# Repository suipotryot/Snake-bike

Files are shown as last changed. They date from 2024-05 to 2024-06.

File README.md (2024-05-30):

# Qu'est ce que c'est ?
Le Snake-bike est un tricycle compact et léger qui permet de rouleur seul et qui peut être accroché à n'importe quel autre Snake-bike, voire même plusieurs, pour devenir un plus grand véhicule. Cela donne une chaîne de vélos articulée qui se déplace telle un serpent, fluide et rapide.

## Pourquoi le Snake bike ?
Le constat généralement fait à propos des transports est que la voiture est omniprésente et qu'il n'y a pas vraiment d'alternative viable. Mais la plupart des réponses à cette problématique sont de nouvelles voitures plus petites, plus légères et électriques ; ou alors de plus gros vélos pour transporter plus de monde, ce qui nécessite également une électrification pour aider le "pédaleur" qui fournit l'énergie pour tout le monde.

Le Snake-bike propose une approche différente : on peut rouler seul et dans ce cas, on ne transporte que son propre véhicule, rien de plus ; mais on peut également rouler à plusieurs sans pour autant s'équiper d'un autre véhicule. Une forme de multi-modalité douce.

En plus de cela, le Snake-bike, outre son cadre spécifique, n'est composé que d'éléments de vélo standards.

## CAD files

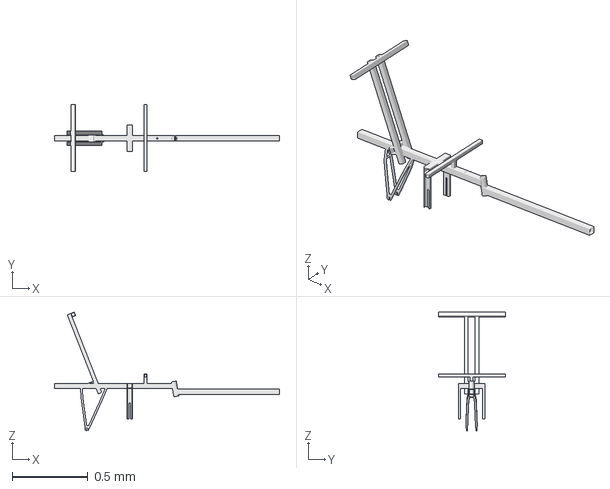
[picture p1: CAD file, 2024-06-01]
Couleuvre.FCStd
1.48 x 0.44 x 0.783 mm

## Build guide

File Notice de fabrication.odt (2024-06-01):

Guide de fabrication du cadre du Snake bike

Modèle Couleuvre – Version Mai 2024

# Le cadre

## Matériel nécessaire

- C1 - tube acier section carrée, diamètre 35 mm, épaisseur 3 mm, L = 1000 mm (partie arrière) ;
- C2 - tube acier section carrée, diamètre 35 mm, épaisseur 3 mm, L = 600 mm (partie avant) ;
- C3 - tube acier section carrée, diamètre 35 mm, épaisseur 3 mm, L = 400 mm (support Nexus) ;
- C4 - tube acier section carrée, diamètre 20 mm, épaisseur 2 mm, L = 500 mm ;
- C5 - tube acier section carrée, diamètre 40 mm, épaisseur 2 mm, L = 105 mm ;
- C6 - tube acier rond, diamètre 34 mm, L= 100 mm (tube de potence standard) ;
- C7 - triangle arrière de vélo 16 pouce en acier.

## Étapes de fabrication

1. Découper les tubes C1 et C2 de manière à ce qu'ils épousent la forme du tube C6 en lui donnant un angle de 10°.
2. Souder les tubes C1 et C2 sur C6 selon le schéma 1. (https://wikixd.fabmob.io/Fichier:SD_Etape_1_-_Soudure_C1_C2_et_C6.png)

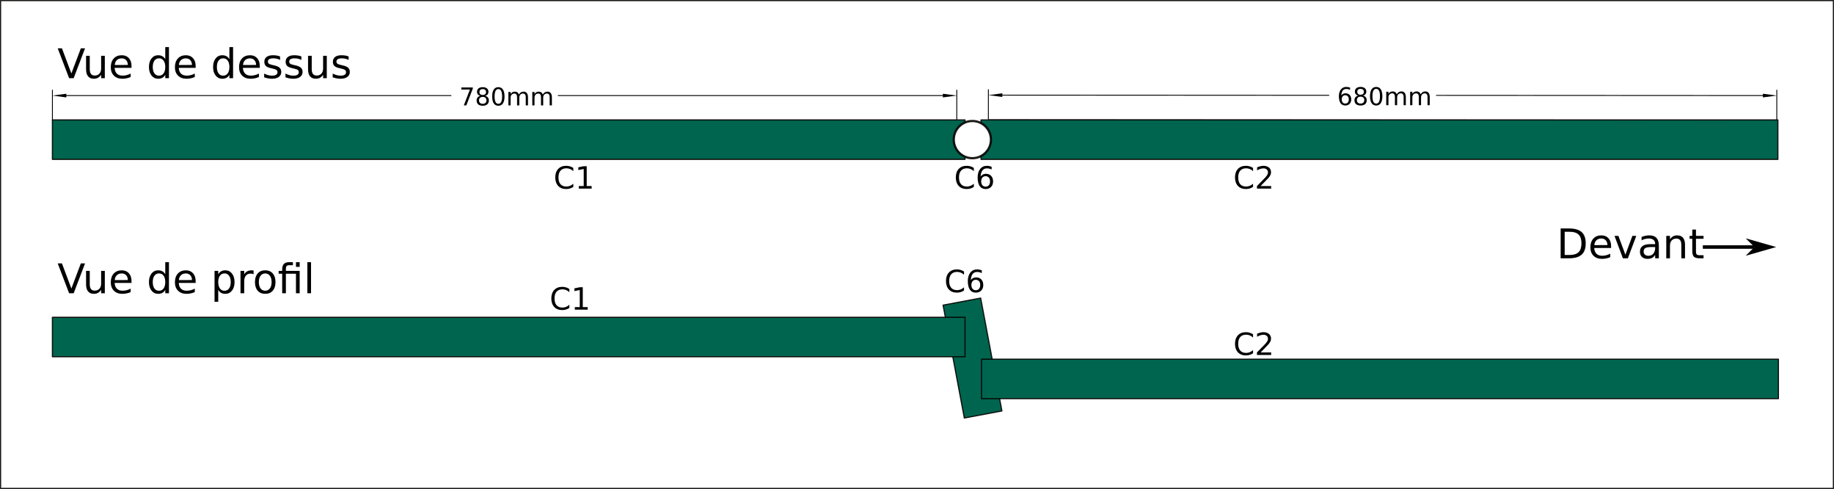
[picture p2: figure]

3. Percer un trou vertical de diamètre 10 mm dans la partie arrière, à ? mm de la potence (pour le guidon).
4. Percer un trou horizontal de diamètre 10 mm dans la partie arrière, à ? mm de la potence (pour la partie arrière du siège).
5. Percer deux trous de diamètre 8 mm dans la partie avant, à 385 mm de la potence (pour le support de pédalier). Cette distance est adaptée à quelqu’un de plutôt grand (1m80) et est à adapter.
6. Percer deux trous de diamètre 10 mm dans la partie avant, à ? mm de la potence (pour le tendeur de chaîne).
7. Percer un trou de diamètre 18 mm dans la partie arrière à 640 mm de la potence. Ce trou servira à fixer la boule de remorquage.

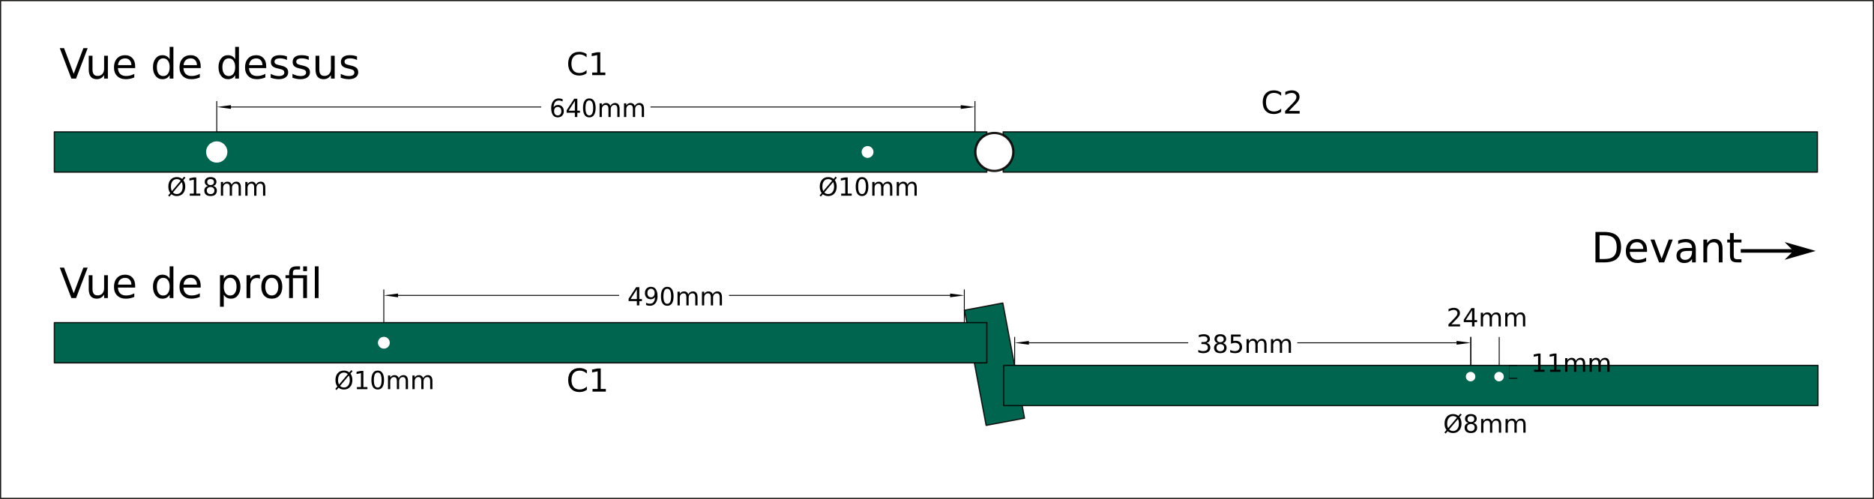
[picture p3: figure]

  (https://wikixd.fabmob.io/Fichier:SD_Etape_2_-_Trous_C1_et_C2.png)
8. Souder le triangle de vélo C7 sur la structure. (https://wikixd.fabmob.io/Fichier:SD_Schéma_3_-_Soudure_triangle_vélo.png)

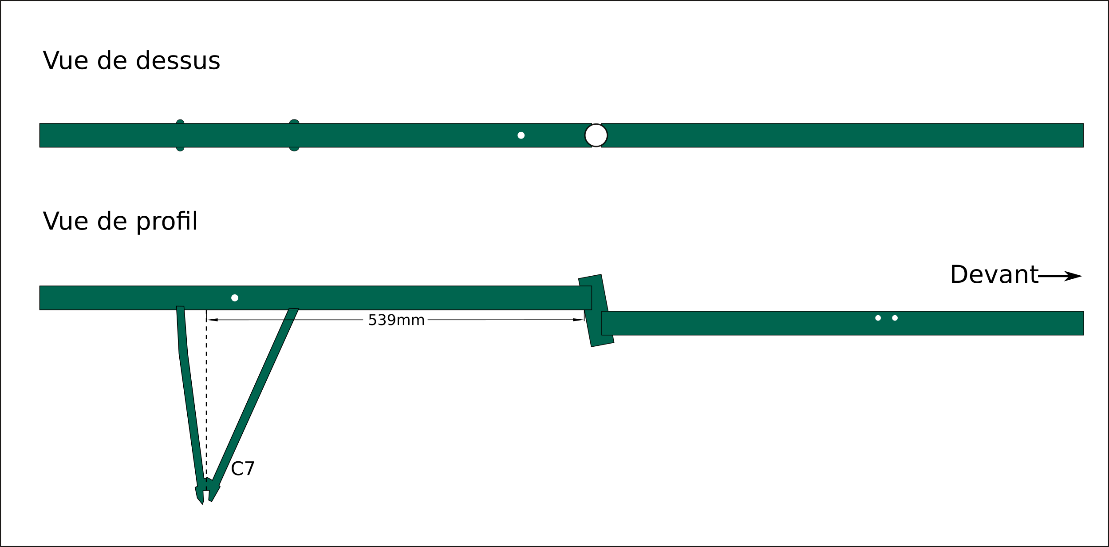
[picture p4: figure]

9. Découper le tube C4 en une section de 440 mm et une de 40 mm. Les souder en formant un "T".
10. Souder ce "T" sur le cadre à 160 mm de la potence. (https://wikixd.fabmob.io/Fichier:SD_Schéma_4_-_Soudure_T_du_siège.png)

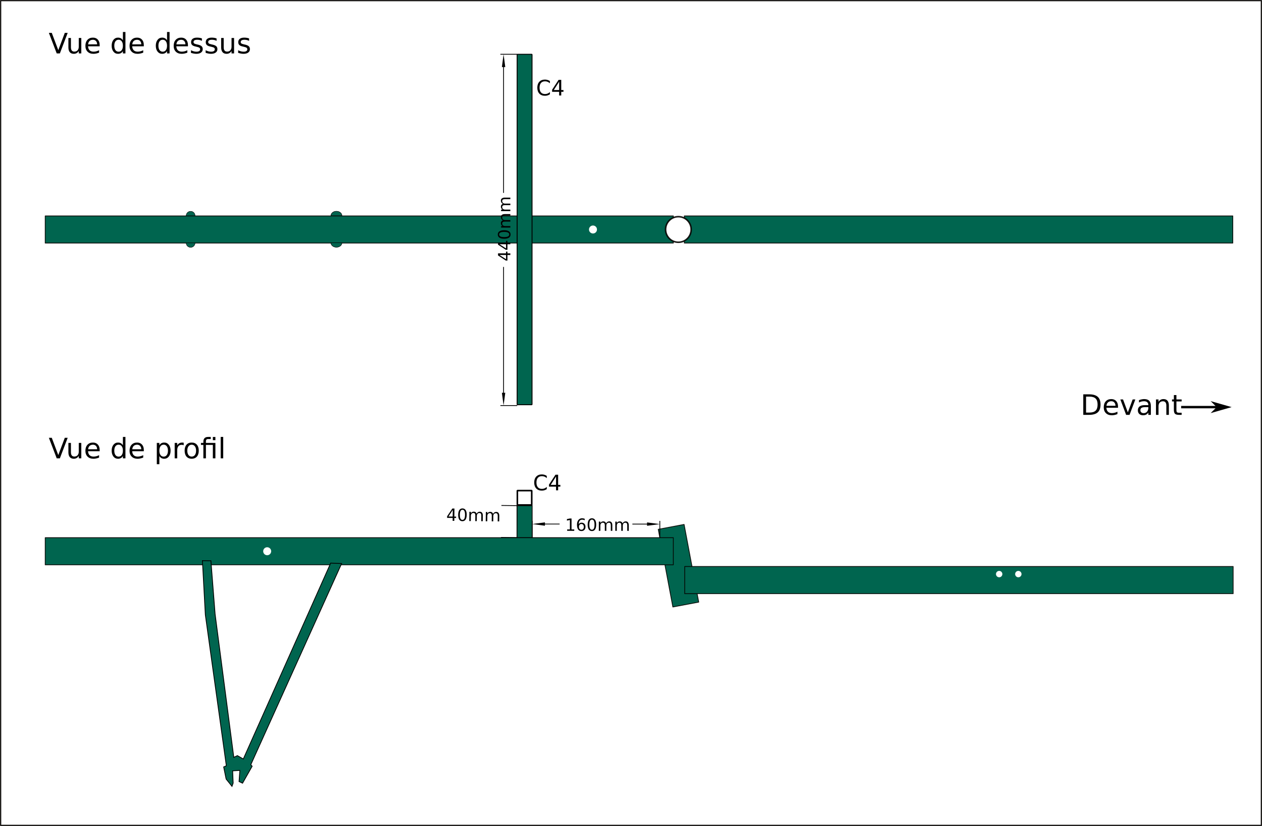
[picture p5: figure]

11. Découper le tube C5 sur la longueur pour obtenir un "L" qui servira de butée au siège.
12. Souder ce "L" sur le cadre. (https://wikixd.fabmob.io/Fichier:Schéma_5_-_Soudure_butée_du_siège.png)

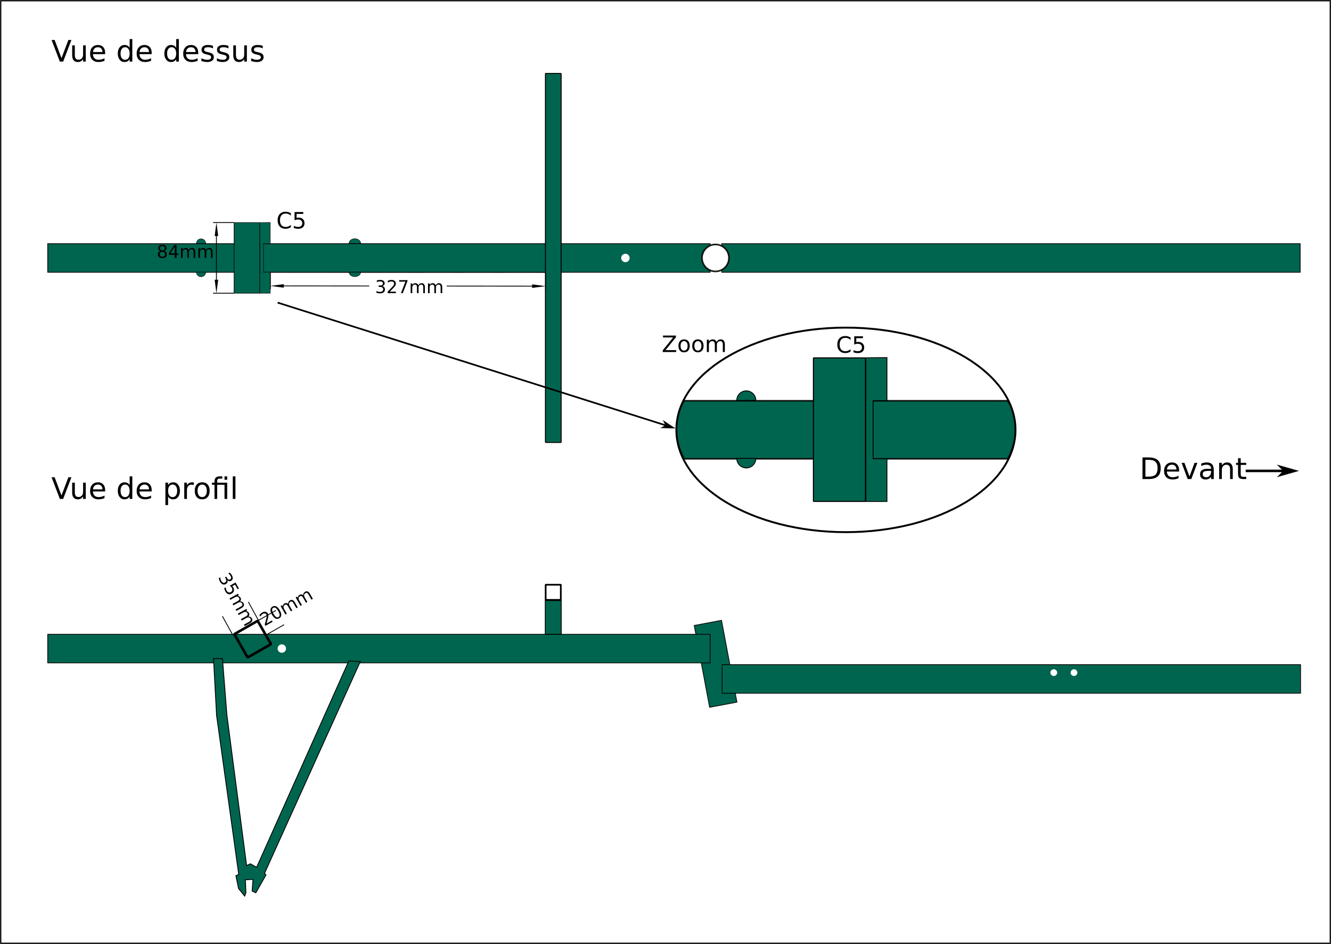
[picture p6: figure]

13. Découper le tube C3 en deux parties de 70 mm et une de 200 mm.
14. Couper la partie de 200 mm en deux sur la longueur et y découper une entaille de 10 mm de large sur deux tiers de sa longueur, en son centre (cela permettra de régler la position du Nexus).
15. Souder le tout sur le cadre pour qu'il y ait un écart de 133 mm entre les deux pièces verticales.

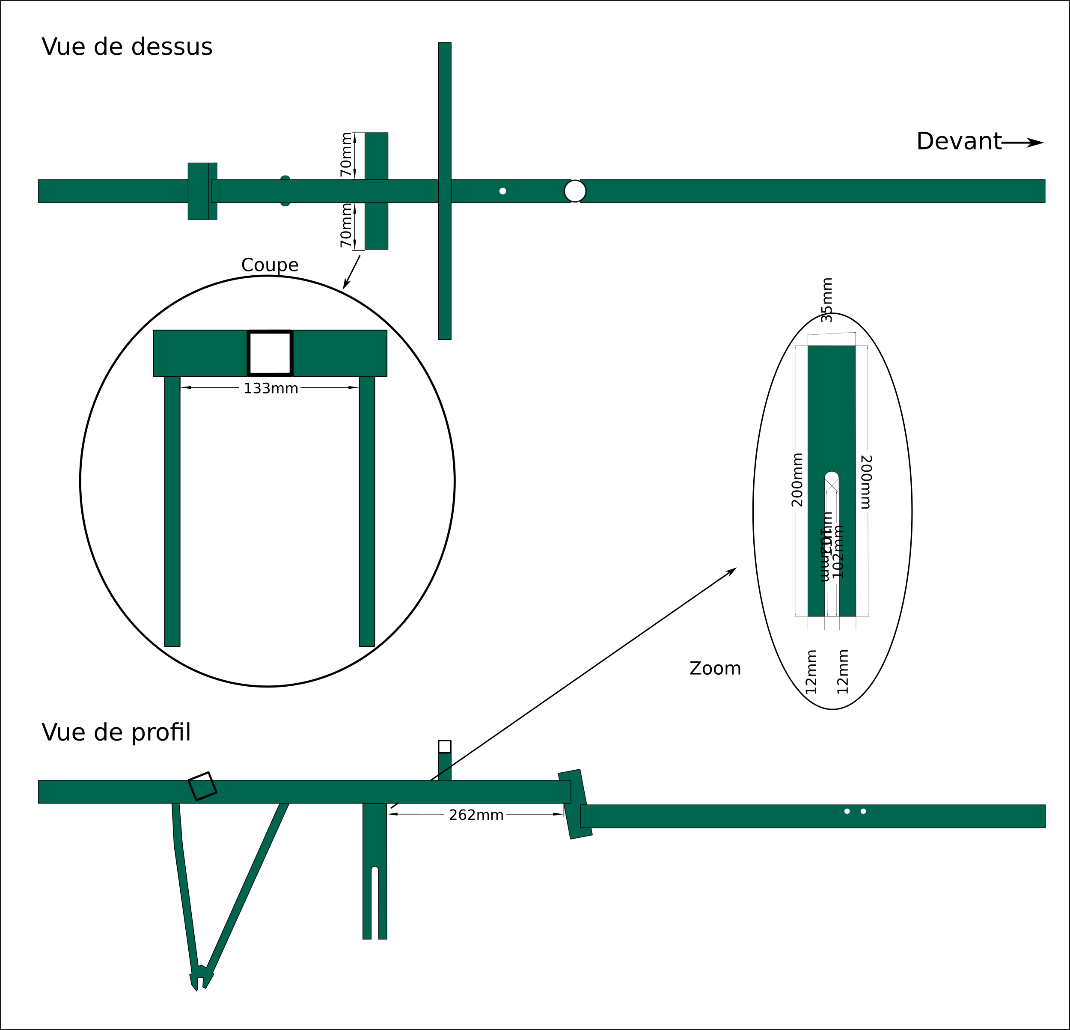
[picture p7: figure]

  (https://wikixd.fabmob.io/Fichier:SD_Schéma_6_-_Soudure_structure_Nexus.png)

Voilà ! Après ces étapes, le cadre est terminé et on en a presque fini avec les soudures.

# Direction - Guidon

## Matériel nécessaire

- G1 - tube acier section rectangle, diamètre 20x30 mm, épaisseur 2 mm, L = 600 mm ;
- G2 - Un guidon pour VTT en acier.

## Étapes de fabrication

1. Percer un trou de diamètre 10 mm en centre de G1 (sur le côté de 30 mm).
2. Percer un second trou de diamètre 8 mm à 100 mm du premier.
3. Couper le guidon G2 en deux parties égales.
4. Souder les deux parties de G2 aux extrémités de G1. Bien veiller à ce que les deux parties soient orientées dans le même sens. (https://wikixd.fabmob.io/Fichier:SD_Schéma_7.1_-_Soudure_et_percement_Guidon.png)

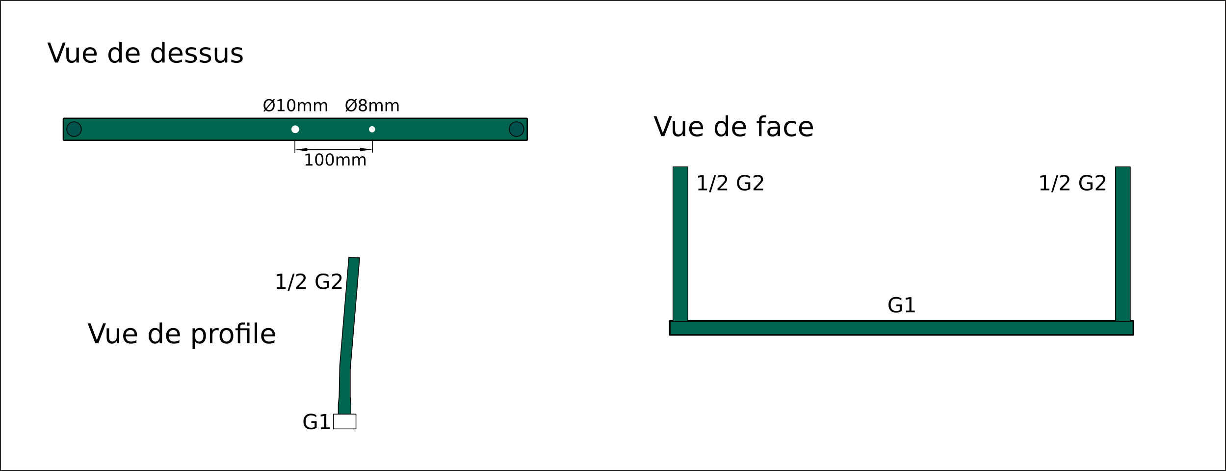
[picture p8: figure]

5. Monter le guidon sur le trou prévu dans le cadre. (https://wikixd.fabmob.io/Fichier:SD_Schéma_7.2_-_Montage_Guidon.png)

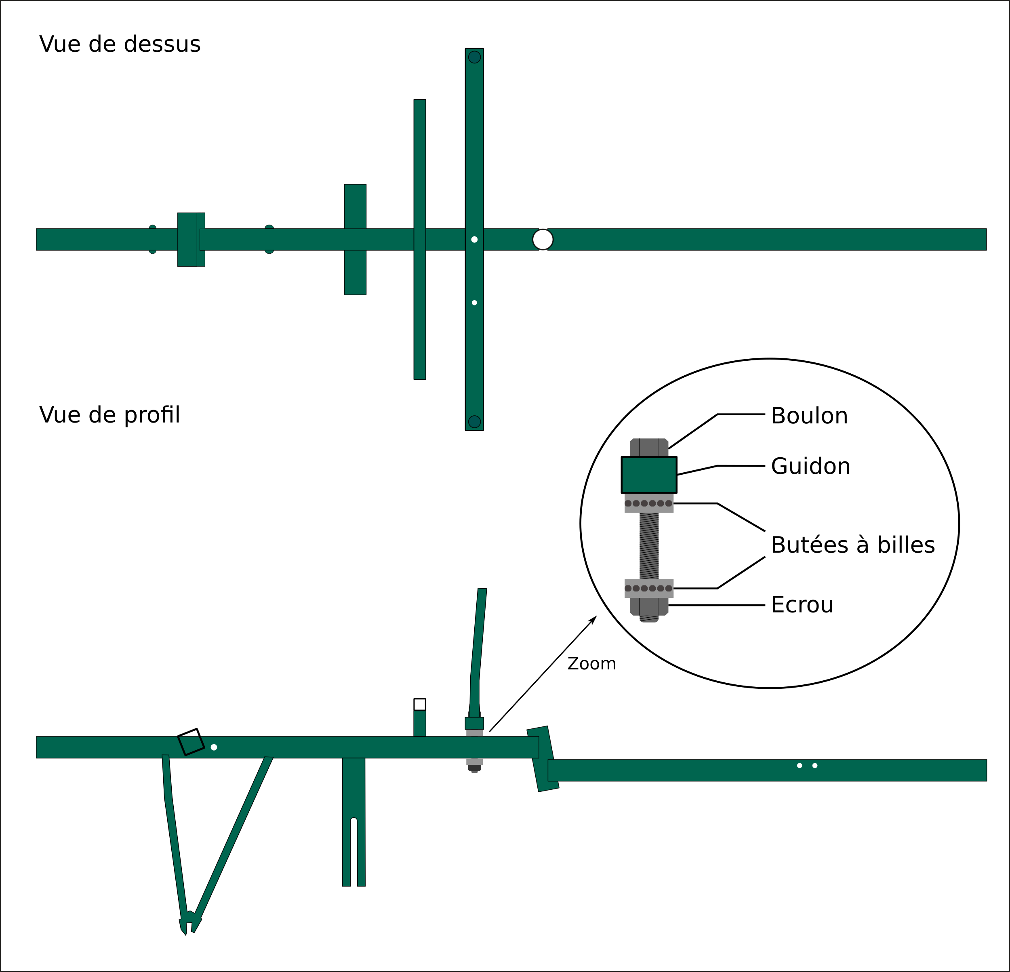
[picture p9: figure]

# Direction - Contrôle

## Matériel nécessaire

- DC1 - Tige de direction se serrant dans la potence.
- DC2 - Barre acier d'épaisseur 5 mm et de largeur 25 mm, L = 100 mm.

## Étapes de fabrication

1. Couper la tige DC1 pour avoir 90 mm entre la pointe et le bord.
2. Souder la barre DC2 sur la partie droite de la tige DC1.
3. Percer de trous de diamètre 8 mm dans DC2, un au milieu de là ou est soudée DC1 et l'autre 70 mm plus loin.

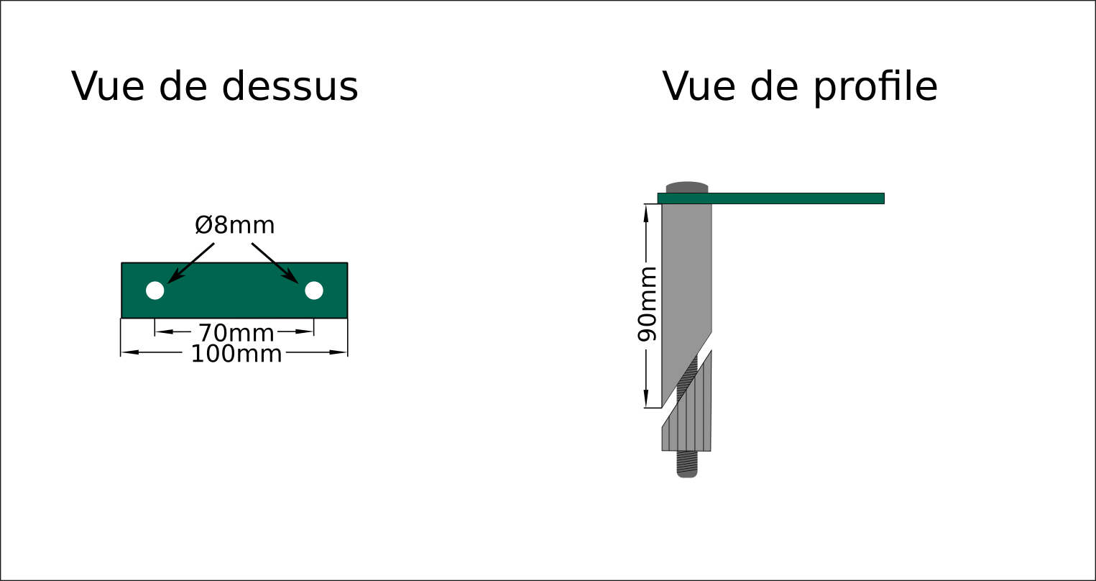
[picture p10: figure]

(https://wikixd.fabmob.io/Fichier:SD_Schéma_8_-_Soudure_contrôle_de_direction.png)

# Direction - Montage

## Matériel nécessaire

- DM1 - Rotule DIN de diamètre 8 mm.
- DM2 - Rotule TSF de diamètre 8 mm.
- DM3 - Deux butées à billes de diamètre intérieur 10 mm.
- DM4 - Un boulon de diamètre 10 mm et de longueur ? mm.
- DM5 - Un écrou à arrêt pour boulon de 10 mm.
- DM6 - Un boulon de diamètre 8 mm et de longueur 40 mm.
- DM7 - Un écrou à arrêt pour boulon de 8 mm.
- DM8 - Tige filetée diamètre 8 mm, L = 80 mm.

## Étapes de fabrication

1. Fixer le guidon de direction sur le cadre grâce au boulon DM4 en faisant un sandwich : Guidon / butée à bille DM3 / cadre / butée à bille DM3 / écrou d'arrêt DM5.
2. Fixer la rotule DIN DM1 dans le trou du contrôle de direction.
3. Fixer la rotule TSF DM2 dans le trou du guidon avec le boulon DM6 et l'écrou DM7.
4. Relier les deux rotules avec la tige filetée DM8.

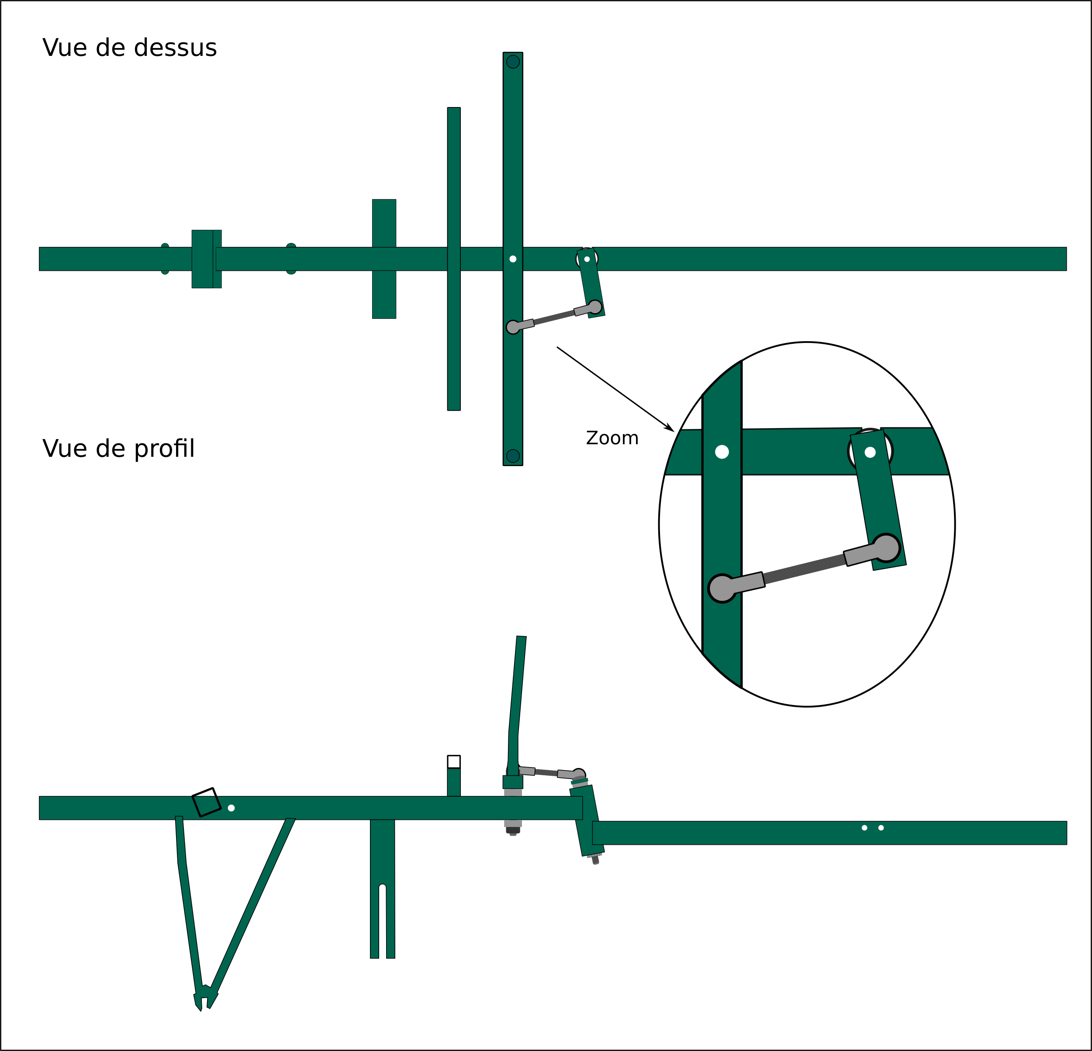
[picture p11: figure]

(https://wikixd.fabmob.io/Fichier:SD_Schéma_9_-_Rotules_de_direction.png)

La direction est prête \o/.

# Siège

## Matériel nécessaire

- S1 - 2 tubes alu carré diamètre 25 mm, L = ? mm.
- S2 - Tube alu carré diamètre 25 mm, L = 440 mm.
- S3 - 2 boulons + écrous + rondelles 5*60 mm.
- S4 - Boulon 10*120 mm + écrou.
- S5 - Deux butées à billes de diamètre intérieur 10 mm.
- S6 - Tissu pour chilienne, 800 x 440 mm.
- S7 - Rivets 3 mm.

## Étapes de fabrication

1. Percer les deux tubes S1 en bas en 10 mm et en haut en 6 mm.
2. Percer deux trous dans le tube S2 en diamètre 6 mm à 180 mm de chaque côté.
3. Boulonner les trois tubes ensemble.
4. Fixer au cadre avec le boulon S4 et les deux butées à bille S5. (https://wikixd.fabmob.io/Fichier:SD_Schéma_10.1_-_Tubes_de_siège.png)

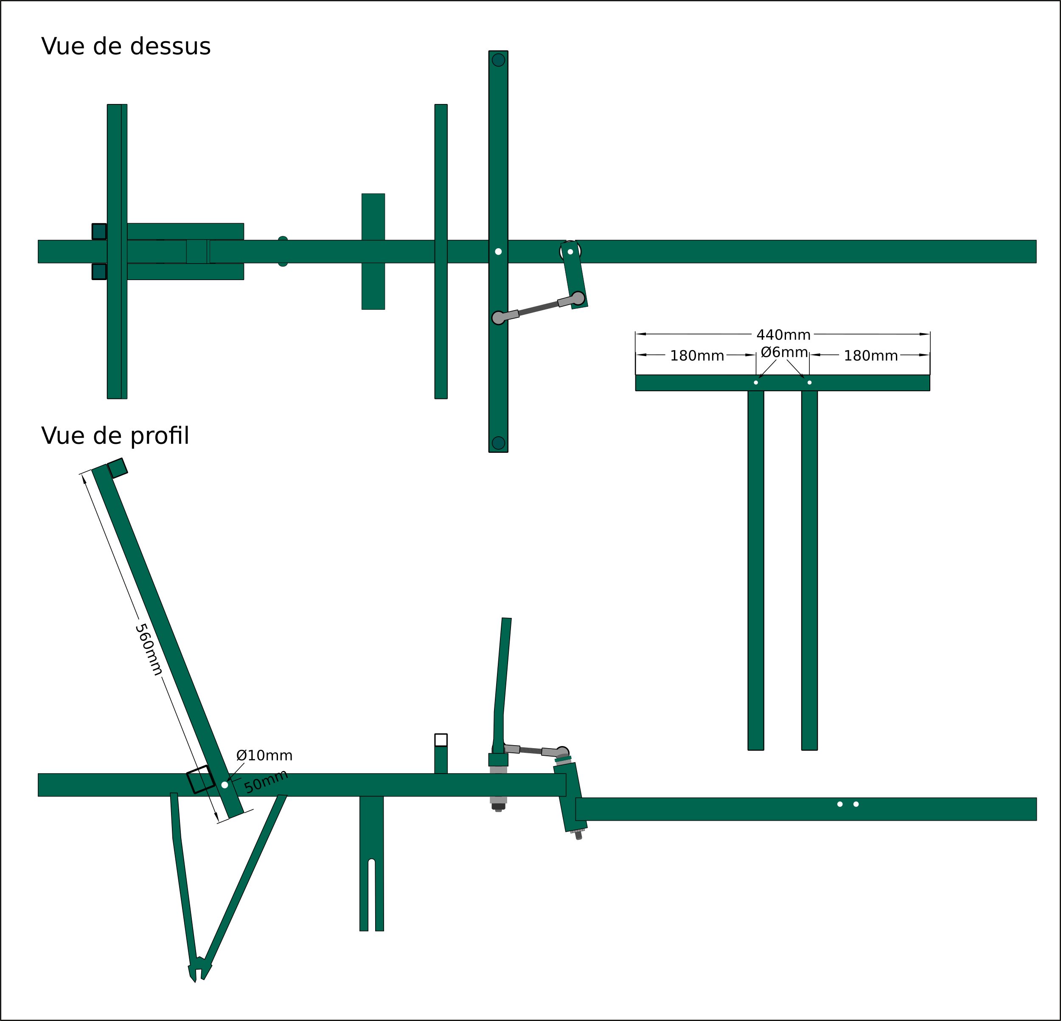
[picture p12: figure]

5. Riveter le tissu S6 avec les rivets S7 de part et d'autre du support de siège. (https://wikixd.fabmob.io/Fichier:SD_Schéma_10.2_-_Tissu_de_siège.png)

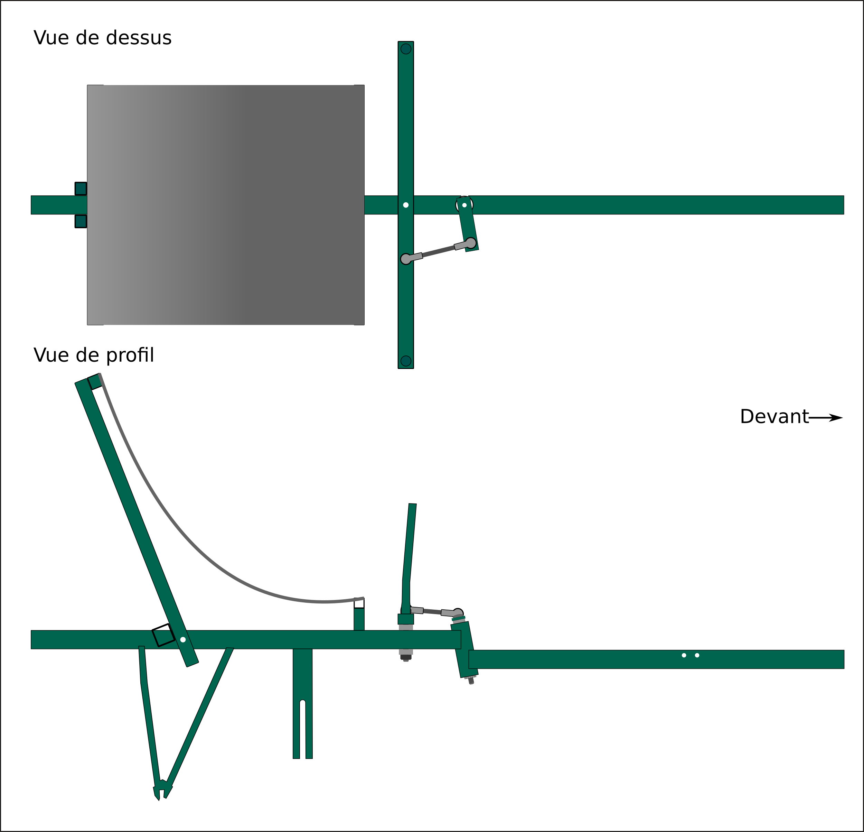
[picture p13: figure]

# Propulsion

## Matériel nécessaire

- P1 - Kit pour tricycle.
- P2 - Boulon + écrous diamètre 10 mm, L = ? mm.
- P3 - Boulon + écrous diamètre 10 mm, L = ? mm.
- P4 - Nexus inter 8 ou moins, selon les goûts).
- P5 - pignon de pédalier récupéré de 28 dents.
- P6 - boulons 3x10 mm + écrous + écrous d'arrêt.
- P7 - Support pour pédalier.
- P8 - Pédalier.
- P9 - 2 chaînes de vélo.

## Étapes de fabrication

1. Installer le kit P1 grâce aux boulons P2 et P3. Régler l'écart avec des écrous.
2. Découper le pignon P5 pour pouvoir le fixer au Nexus (c'est l'étape la plus fastidieuse de la fabrication).
3. Percer le pignon P5 en s'assurant de bien l'aligner avec les trous du Nexus (utiliser un patron en carton).
4. Fixer le pignon au Nexus via les boulons P6 en mettant à chaque fois 3 petits écrous entre le Nexus et le pignon.
5. Monter la cassette du Nexus en veillant bien à mettre le pignon du Nexus vers l'extérieur (pour l'éloigner le plus possible du pignon fait maison).
6. Installer le Nexus sur le cadre, cassette vers le bas.
7. Boulonner le support P7.
8. Fixer le pédalier P8 sur P7.
9. Installer une chaîne de vélo P9 entre le pédalier et le pignon d'origine du Nexus.
10. Installer la seconde chaîne P9 entre le pignon fait maison P5 du Nexus et le kit pour tricycle P1.

Après ajout des éléments de cycle (freins, levier de vitesse, gaines et câbles associés), le Snake est prêt pour rouler en solo !

Attention néanmoins, la version solitaire du Snake bike est un peu déséquilibrée et n’est pas faite pour de grandes vitesses ni des virages trop serrés.

# Système de chaînage

## Matériel nécessaire

- CH1 - Boîtier d'attelage pour tube carré 50 mm
- CH2 - Rotule spéciale quad diamètre 50 mm.

## Étapes de fabrication

1. Fixer CH1 à l'avant du Snake.
2. Fixer CH2 à l'arrière.

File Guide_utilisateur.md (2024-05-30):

# Guide de l’utilisateur du Snake-bike

## Avant propos

À l’heure actuelle, le Snake-bike reste à l’état de prototype. Son utilisation n’a pas encore été suffisamment éprouvée pour permettre d’assurer sa fiabilité, notamment pour des vitesses supérieures à 15km/h et pour de longues distances.

Bien que particulier et original, le Snake-bike est un vélo à part entière. Il entre légalement dans la catégorie des cycles, que l’on retrouve officiellement dans l’article R311-1 du code de la  route (https://www.legifrance.gouv.fr)
« 6.10. Cycle : véhicule ayant au moins deux roues et propulsé exclusivement par l’énergie musculaire des personnes se trouvant sur ce véhicule, notamment à l’aide de pédales ou de manivelles. »

## Réglementation

Même s’il est auto-construit, il est tout à fait autorisé de rouler sur a voie publique en Snake-bike. Il y a néanmoins plusieurs réglementations dont il faut être conscient et qu’il faut respecter.

### Voies autorisées

Le Snake-bike étant un cycle, il possède les mêmes autorisations et limites que les vélos classiques, à savoir :
- Aucun permis de conduire n’est obligatoire pour rouler en Snake-bike.
- Il peut rouler sur les pistes cyclables, d’autant plus qu’il ne fait que 70 cm de large.
- Il peut également rouler sur toute route qui ne lui est pas interdite :
  - Les autoroutes et voies rapides également sont strictement interdites aux cyclistes.
  - Plus généralement, les routes dont la limitation est de 110 km/h à 130 km/h sont interdites. 
- Il peut utiliser les chemins de vélo.
- Enfin il est interdit de rouler sur les trottoirs.

### Équipements obligatoire

Le Snake-bike doit être équipé, au minimum des éléments suivants :
- Deux freins, avant et arrière.
- Des catadioptres (dispositifs retro-réfléchissants) à l’avant, à l’arrière, sur les pédales et sur les côtés (dans les roues).
- Des feux de position : jaune/blanc à l’avant et rouge à l’arrière.
- Une sonnette.

De plus, quelques règles s'ajoutent :
- Le port du casque est obligatoire pour tout cycliste de moins de 12 ans. Et il est fortement conseillé pour tous les autres. Ce casque doit être attaché.
- Le port du gilet retro-réfléchissant est obligatoire pour tout cycliste circulant hors agglomération la nuit ou lorsque la visibilité est insuffisante.
- Il est interdit de téléphoner en roulant ou même d’avoir un casque audio, des écouteurs ou des oreillettes.

## Vitesse maximale

En solitaire (i.e. lorsque vous roulez seul sur un seul Snake-bike non chaîné), il est fortement conseillé de rouler relativement lentement, à savoir moins de 15 km/h et de prendre vos virage à faible vitesse, afin d’éviter tout basculement du véhicule.

Dans le cadre d’un chaînage (i.e. au moins deux Snake-bikes chaînés), cette restriction ne s’applique plus car il n’y a alors plus de risque de basculer.

Le pilote d’une chaîne (i.e. le cycliste qui conduit le Snake-bike en première place dans la chaîne) doit porter une attention particulière à la trajectoire que prennent les Snake-bikes qui lui sont accrochés. Bien que le système d’articulation assure une trajectoire similaire pour tous les véhicules chaînés, les virages trop serrés ainsi que les passages étroits sont fortement déconseillés.

## Règles de sécurité

- Il ne faut JAMAIS laisser un enfant SEUL sur un Snake-bike.
- Serrer le frein parking avant de descendre. Et ne pas laisser l’engin, non calé, orienté dans une pente, en marche avant ou arrière
- Ne jamais mettre les pieds au sol pendant le roulage, sous risque de blessures grave, surtout dans une chaîne de Snake-bike (qui implique une plus forte inertie du véhicule).
- Avant chaque utilisation, il est important de procéder à quelques vérification :
  - Gonflement des pneus (avant et arrière).
  - Fonctionnement des freins (avant et arrière).
  - Tension des chaînes.

## Déplacement manuel et marche arrière

Pour déplacer le Snake-bike ou pour faire une marche arrière (qui n’est pas possible en pédalant), procéder aux étapes suivantes :
    1. tenir la poignée de l’attache remorque à l’avant du véhicule ;
    2. déverrouiller le frein sur la poignée ;
    3. soulever la roue avant pour déplacer facilement le Snake-bike ;
    4. une fois le déplacement terminé, remettre le frein de parking.

## Rangement
Pour ranger le Snake-bike, le plus efficace est de le positionner verticalement. Ainsi il n’occupera au sol que 70x70 cm. Pour ce faire, procéder aux étapes suivantes :
    1. s’assurer qu’aucun obstacle n’est présent derrière le Snake-bike ;
    2. tenir la poignée de l’attache remorque à l’avant du véhicule ;
    3. déverrouiller le frein sur la poignée ;
    4. soulever la roue avant jusqu’au basculement du Snake-bike.

Lors d’un rangement, il est conseillé de positionner le Snake-bike vertical contre un mur, le siège face au mur, les roues vers l’extérieur. Cette position assure que le Snake-bike ne basculera pas à cause d’un choc.

## Entretien

Dans le cadre d’un entretien ou d’une réparation, il est conseillé de mettre le Snake-bike dans sa position de rangement vertical afin d’avoir facilement accès à l’ensemble des composants (roues, câbles, chaînes, freins, etc).
